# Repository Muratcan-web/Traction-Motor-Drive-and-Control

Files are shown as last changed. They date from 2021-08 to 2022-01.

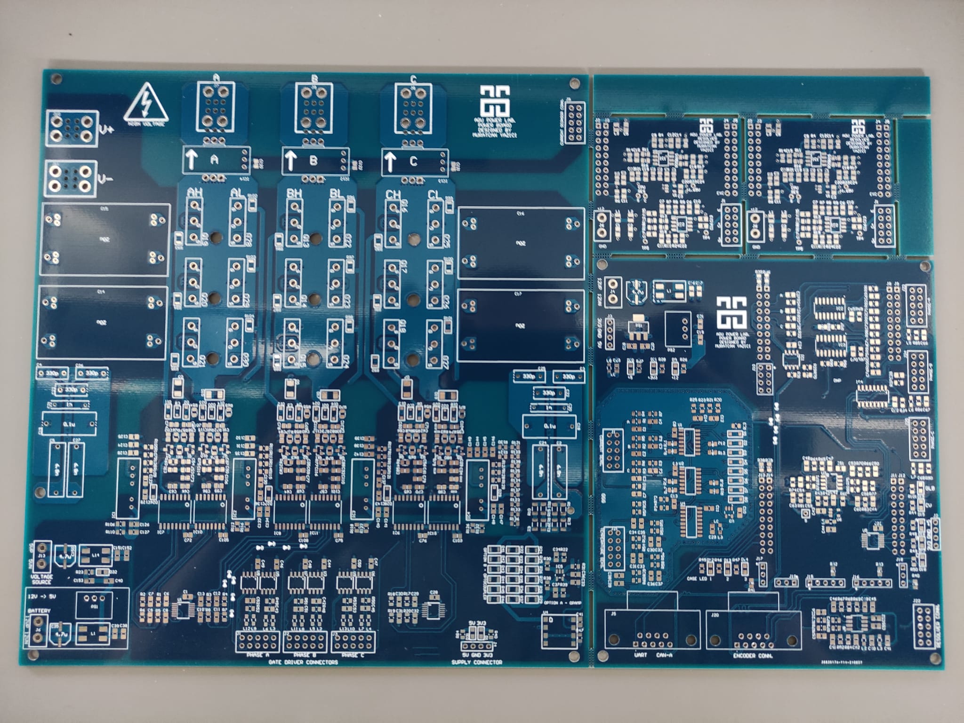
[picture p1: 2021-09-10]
pcb.jpeg

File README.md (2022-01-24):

# Traction-Motor-Drive-and-Control
In this project, I worked on the Control and Power Boards of a Traction Motor Drive system. The drive system is capable of controlling upto 36kW AC Induction Motors. 

You can find the required circuits and layout of the system in this repository. The detailed explanations of the firmware can be found in "TMD Final Report.pdf" document. 

If you have any questions and suggestions, please do no hesitate asking: muratcann.yazici@gmail.com

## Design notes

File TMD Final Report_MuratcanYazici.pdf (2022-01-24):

# Traction Motor Drive Design and Control

Muratcan Yazici
Electrical Electronics Engineering Abdullah Gul University
muratcan.yazici@agu.edu.tr

Dr. Burak Tekgün
Electrical Electronics Engineering Department Abdullah Gul University
burak.tekgun@agu.edu.tr

Abstract— This paper reports a detailed description of a Drive and Control system for Traction Motors. The hardware and software configurations, details and the working principles of each stage are explained in detail.

Keywords— AC Motors, Drive and Control Systems, PI Control, F28379D, PCB Design.

1. INTRODUCTION
Motor drivers act as an interface between the power source and the motor and mainly adjust the speed of the employed motor. These devices provide the users with process control and energy conservation. The aim of an AC Motor Drive is to drive a 3-Phase AC motor. To drive 3-phase motors, “Variable Frequency Drives (VFD)” are employed. VFDs convert an incoming 3 Phase voltage into a variable frequency 3 Phase output and drive AC Motors. The block diagram of a VFD is shown in Figure 1.1.

Figure 1. 1: VFD Block Diagram

In such systems, the first step is to make the AC/DC conversion. The rectifier fulfills this duty. Then, the DC link further filters the rectified voltage and delivers a pure DC voltage to the inverter stage. The inverter converts the DC voltage in to a controlled AC voltage to provide the user with the control of the AC motor torque, speed and position.

In this particular project, the input power is directly a DC voltage. It can be thought of an electric vehicle battery pack. Thus, the rectifier stage in Figure 1.1 is not populated. The particular block diagram of the “Traction Motor Drive Design and Control” project is shown in Figure 1.2.

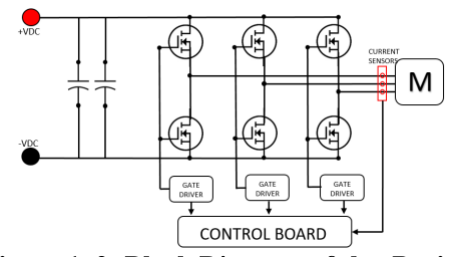
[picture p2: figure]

Figure 1. 2: Block Diagram of the Project

As can be seen from the block diagram, the incoming DC voltage is filtered, and then converted into variable frequency AC voltage at the inverter stage. The inverter is designed using IXFH42N60P3 N-Channel high power MOSFETs. Each phase is controlled by two MOSFETs, and AC output is produced based on the switching of these devices. The switching application of the MOSFETs is controlled by Gate Driver circuits. These circuits take PWM signals from the Control Board and provide the MOSFETs with required switching signals. Thus, the control of the motor is completed with the control signals coming from the control board.

There are Current Sensors (LEM-25) at the input of the motor to check the amount of current that motor uses. The current values for phase A and C are fed back to the control circuit, and the required precautions are calculated and carried out.

The aforementioned process is divided into two PCB boards: Power Board and Control Board. These boards consists of the circuits in Table 1.1. Each of these circuits is explained thoroughly in the following sections.

Control Board | Drive Board
1) Fault Circuit | 1) Bus Voltage Filter
2) Power Supply Interface | 2) Bus Voltage Sense Circuit
3) Current Sensor Interface | 3) Gate Driver Fault Circuit
4) Voltage Sensor Interface | 4) Isolated DCDC Converter Stage for Gate Drivers
5) Temperature Interface | 5) Gate Driver Circuit
6) CAN Interface | 6) Mosfet Connections
7) F28379D Launchpad
8) Gate Driver Interface
9) Resolver Interface
Table 1.1: The contents of each PCB

2. CONTROL BOARD CIRCUIT EXPLANATIONS
2.1. Fault Circuit

This circuit is implemented to shut the operation of the Motor Driver in case of a Over Current or Over Voltage failure. This circuit is used as an external fault detection application in which the current measurements from the current sensors and the DC Bus voltage are checked. This operation is carried out using quadrature comparators, particularly LM339.

The current sensor (LEM LES25-NP) will output a voltage between 0.25V and 4.75V, which represent -85A and +85A respectively. For instance, if the amplitude of the current output is desired to be between -20A and +20A, the output voltages should be in the range of 2V and 3V. The Voltage/Current output graph of the current sensor (LES 25 NP) is depicted in Figure 2.1.1.

Figure 2.1. 1: Voltage/Current relationship of LES 25NP

: Primary Nominal RMS Current (25A)
: Primary Current Measuring Range (-85A to 85A)

Based on the requirement (the currents should not exceed -20A to 20A range) that the output of LES25 should be between ~2V and ~3V, a circuit was built that produces a FAULT signal if the voltage is not in the aforementioned range. To build this circuit, LM339, a low-power comparator is selected. With this device, four different conditions can be analyzed simultaneously. The pin diagram of LM339 is shown in Figure 2.1.2.

Figure 2.1. 2: Pin Diagram of LM339

Comparator circuits simply compare two voltages. The output of such a device is digital (either HIGH or LOW) depending on the voltage values of the inverting and non-inverting inputs. The principle of the operation is that if the voltage value at the inverting input (-) is greater than the non-inverting(+) input, the output is LOW, and vice versa.
The output of the comparator circuit results in a signal, meaning that FAULT = LOW, NO-FAULT = HIGH. The cases are as follows: (Refer to Figure 1.1.5 for the schematic)
- If the output voltage of a Current Sensor (IX_Filtered) is less than LowLimit (2V), which is a faulty case, the output of that condition will be LOW. If IX_Filtered is higher than the LowLimit, which is a non-faulty case, the output will be HIGH.
- If the output voltage of a Current Sensor (IX_Filtered) is less than HighLimit (3V), which is a non-faulty case, the output of that condition will be HIGH. If IX_Filtered is higher than the HighLimit, which is a faulty case, the output will be LOW.

The desired input/output table is shown in Table 2.1. To simulate this operation, the circuit shown in Figure 2.1.3 was set on Proteus, and simulated. The simulation result is shown in Figure 2.1.4.

IX_Filtered (V) | Fault
2< V < 3 | No
3 < V | Yes
V < 2 | Yes
Table 2.1: Desired Current Fault Cases

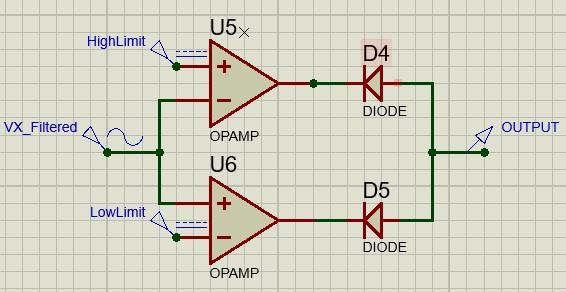
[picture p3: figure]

Figure 2.1. 3: The simulated circuit

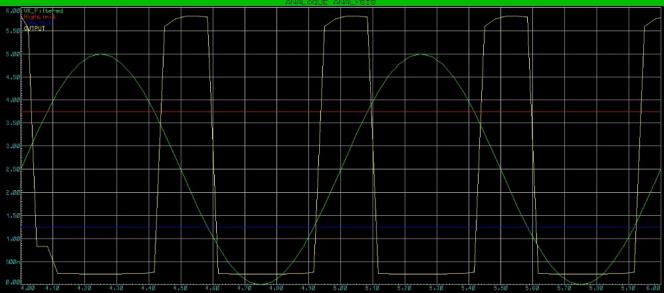
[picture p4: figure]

Figure 2.1. 4: Simulation Results

When IX_Filtered (Green) is in the range of non-faulty voltages, the output (Yellow) is HIGH, else it is LOW. Following this logic, the circuit shown in Figure 2.1.5 and Figure 2.1.6 are designed. In case either one of the fault checks is not needed, the DNP resistors will be populated to create automatically non-fault (HIGH) output.

Figure 2.1. 5: A and B phase Fault Circuit

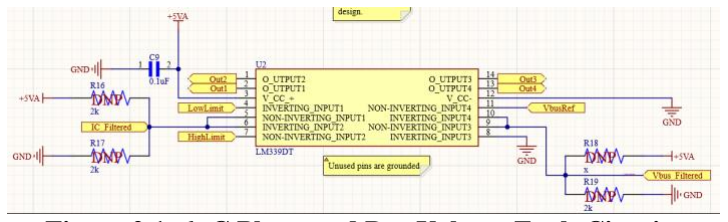
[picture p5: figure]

Figure 2.1. 6: C Phase and Bus Voltage Fault Circuit

In case the control is not required, the resistors must be populated to generate a DC voltage (Voltage divider) in high and low limits so that a non-faulty case will be automatically obtained.

If a VBUS fault check is not required, populating R19 will be enough to disable this function. On the design, the VBUS error limit is 280V. This limit can be arranged.

The reference voltages for the comparator circuit are obtained using the following voltage divider circuitry shown in Figure
2.1.7. The values are only for example, not for the current design. The voltage level must be adjusted to satisfy the need.

Figure 2.1. 7: Reference Voltage Divider Stage

The outputs of the comparator circuits must be connected to Diodes. The reason for that is, when there is a FAULT case, the main fault signal will be tied to the ground. If there is a no-fault case, there will not be a voltage drop on the pull-up resistor shown in Figure 2.1.8 and the input to the inverter will be high. Moreover, since the output of the comparator circuit
is | , an inverter is required for the SR-Latch input. SR-
Latch is required for shutting down the PWM signals, and keeping them shut down until the reset signal (SR-Reset) is sent.

Figure 2.1. 8: Comparator Outputs and Inverter Circuit

At the output of the inverter is a FAULT signal, which is connected to the SR Latch (HEF4043BT). The SR Latch output is connected to Differential Line Driver Enable input for the PWM signals to shut down the operation in case of a failure. The SR Latch Connections are shown in Figure 2.1.9.

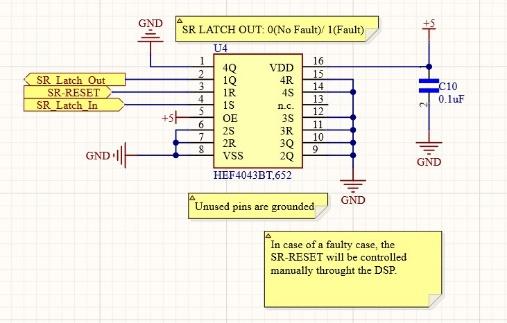
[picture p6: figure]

Figure 2.1. 9: SR Latch Connections

The reset signal is controlled through DSP, and the system is restarted after the fault is eliminated.

To sum up, Fault Circuit is used to control the operation conditions based on the current sensor outputs and VBUS voltage. In case of an overvoltage or undervoltage, the operation will be shut down for protecting rest of the circuits.

2.1.1. Functionality Tests of the Fault Circuit

To test this circuit, the Current Sensor control for phase C is eliminated, meaning that the voltage divider resistors are populated and a 2.5V regulated voltage, which is a non-faulty case, is sent to comparators. The functionality test is run for phase A and B current sensor outputs. As mentioned above, the circuit should yield a faulty output if the current sensor outputs a voltage outside the range of 2V-3V. A sinusoidal wave that has the below features is applied to the circuit, and output is examined. The input is Channel 1 (yellow), and the fault circuit output is Channel 2 (blue). The result is depicted in Figure 2.1.10.

Figure 2.1. 10: Oscilloscope View of the Test Setup

As can be seen, when the input voltage is greater than 3V and less than 2V, the output is low. Otherwise, the output is high. The output is connected to an inverter, and connected to the SR-Latch input. Whenever the fault is generated, SR-Latch remains HIGH untill reset.

2.2. Power Supply Interface

This circuit aims to provide the rest of the circuitry with clean and sufficient power. The input to the supply circuit is 12V battery connections. This voltage should be filtered and converted into 3.3V and 5V to provide the ICs with sufficient power.

Firstly, a common mode choke (CMC) is applied to the battery voltage. Common Mode Noise is present on the circuits mainly due to high-frequency switching applications. High-frequency results in a high di/dt ratio which results in higher Electromagnetic Noise. This noise is present on the signal traces and common ground planes, which affects the signals. The contribution of a CMC to the circuit is that it attenuates the common-mode noise. It adds inductance to the power traces to minimize the current ripples. It is used to reduce the EMI components on the power supply. In addition, to reduce the common-mode noise, power traces are kept as close as possible on the layout. The common-mode choke (ACM7060-701-2PL-TL01) connection is shown in Figure 2.2.1.

Figure 2.2. 1: Common Mode Choke Connections

After filtering the battery power, the 12V should be converted into 3.3V and 5V. First, 12V is converted to 5V with a buck converter (R-78E5.0-1.0), then the 3.3V is obtained by an LDO that has the input from the 5V. Here, a great care is paid for the noise on analog and digital circuits on the Control Board. Analog circuits are more susceptible to noise. Thus, an LC filter is applied and the power lines of analog and digital circuits are separated. Voltage conversion and filter circuits are shown in Figure 2.2.2 and Figure 2.2.3.

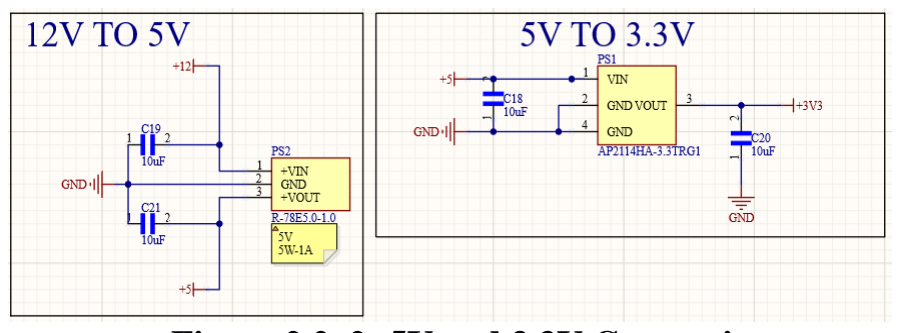
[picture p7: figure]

Figure 2.2. 2: 5V and 3.3V Conversion

Figure 2.2. 3: LC Filter for the Analog Circuits

2.3. Current Sensor Interface

This circuit processes the Current Sensor outputs and sends them to the Fault circuit and DSP. IX_CSensor refers to the output of the current sensor for the associated phase. IX_Filtered is connected to the Fault Circuit for external fault control, and Current-X is connected to DSP. Notice the voltage divider before the Current-X for the protection of the DSP. The current sensor interface circuit is shown in Figure 2.3.1.

Figure 2.3. 1: Current Sensor Interface Circuit

In this part, taking the measurements of two currents will be enough because of Kirchoff’s law. The law ponits out that the sum of the currents entering a node should be zero. Thus:

If the current value for phase A and C is measured, phase B can be reconstructed. Therefore, two current sensors will be enough.

2.4. Voltage Sensor Interface

Voltage values will be found using estimation method from the PWM signals. The XHS_PWM is a modulated signal, and it is demodulated for DSP to read it using the low-pass filter. This circuit is shown in Figure 2.4.1.

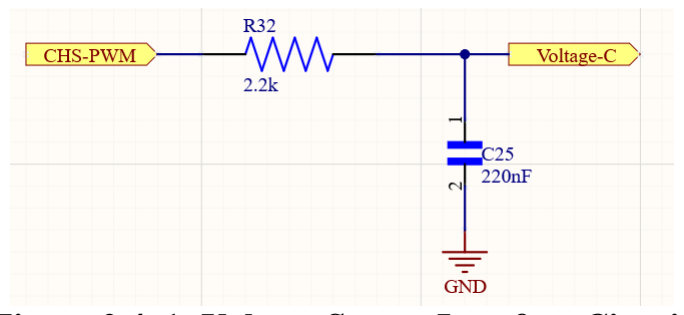
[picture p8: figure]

Figure 2.4. 1: Voltage Sensor Interface Circuit

2.5. Temperature Sensor Interface

This circuit is used to obtain the temperature of Bus capacitors, Bus Bar, and three IGBTs. The output of the thermistor is filtered in the interface circuit and sent to DSP for control. The connector connections of the temperature sensor interface are shown in Figure 2.5.1, and the circuit is shown in Figure 2.5.2.

Figure 2.5. 1: The External Connectors

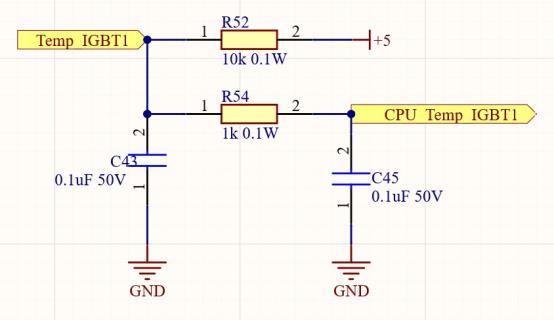
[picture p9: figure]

Figure 2.5. 2: Temperature Sensor Interface Circuit

2.6. CAN Bus Interface

This circuit is used for CAN Bus lines (CANH and CANL) to be converted to TX and RX signals via a CAN Transceiver. The CAN Transceiver connections are shown in Figure 2.6.1.

Figure 2.6. 1: CAN Bus Interface Circuit

CAN Transceivers convert the differential CAN pair (CANH and CANL) into TX (transmit) and RX (receive) signals. CANH and CANL signals are separated from each other by a terminating resistor, 120-ohms. There can not be a direct connection between CANH-L pair and an MCU. Transceivers converts them into TX and RX. TX and RX signals are connected to MCUs (TX to RX/ RX to TX).

2.7. F28379D Connections

The main controller board that sends the control signals to the controller is F28379D Launchpad. The software provides the system with the required signals. It has several connectors on the Launchpad, and requires a couple of hardware configurations.

2.7.1. Global Fault Signal

There are two FAULT circuits in this controller board. The first one is the fault circuit for the current sensor and bus voltage (refer to section 2). The output of this circuit is
CVSense_Fault ( | ).

The second one is the Gate Driver fault outputs (X-FAULT).
These signals are also | In case of faulty case, the
corresponding LEDs will turn ON.

In order to manage all the FAULT signals as one output, a quadrature AND Gate is employed. If any of CVSense_Fault or X-FAULT are faulty (LOW), the AND gate will have LOW signal at the output. This brings us to the conclusion that the
AND Gate output is also | A HIGH signal is generated
only if all the Fault signals are HIGH. The Global Fault circuit is shown in Figure 2.7.1.1.

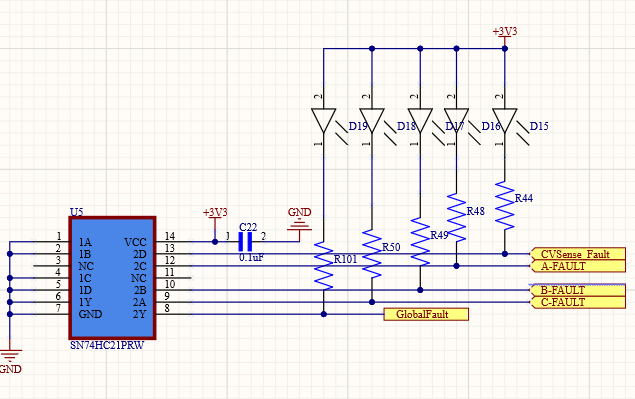
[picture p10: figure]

Figure 2.7.1. 1: Global Fault AND Gate Circuit

2.7.2. DSP Connectors

The Connector designators on Altium Schematics and the actual designators on Launchpad do not match. See the notes next to the connectors to locate the actual connectors on the DSP. In Figure 2.7.2.1, the connectors for Quadrature encoders, ground, and CAN-B Bus connections are presented. For all the power connections (3.3V, 5V), 0-ohm DNP resistors are placed. The reason for these DNP resistors is that the DSP will be either powered by the USB cable provided in the package or the power line from the power circuit. When the DSP is powered by the USB cable, the power from an external circuit is not necessary, thus the DNP resistors shall not be populated. In case it is desired to power the DSP by the power supply existing on the board, the 0-ohm resistors must be populated.

Figure 2.7.2. 1: QEX and Power Connections

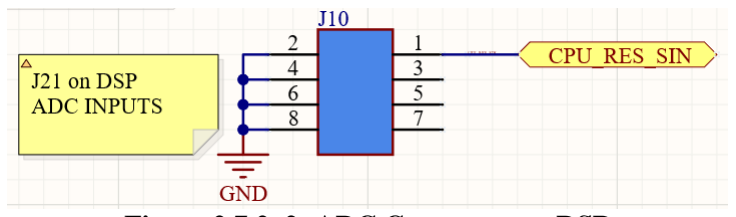
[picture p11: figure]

Figure 2.7.2. 2: ADC Connector on DSP

Figure 2.7.2. 3: AUX Connector

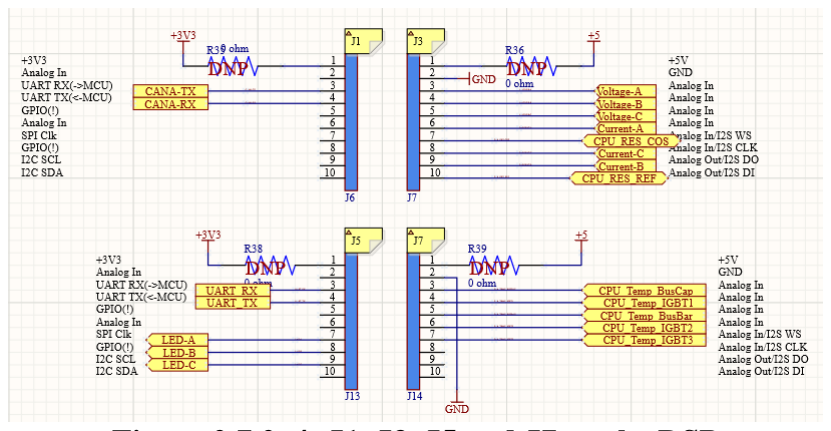
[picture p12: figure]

Figure 2.7.2. 4: J1, J3, J5 and J7 on the DSP

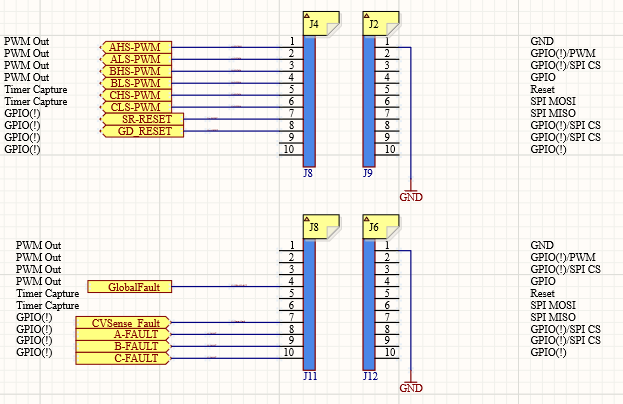
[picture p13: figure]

Figure 2.7.2. 5: J4, J2, J8 and J6 on the DSP

2.8. Gate Driver Interface Circuit

Signal integrity has the utmost importance when controlling power devices with a gate driver. Gate drivers are susceptible to EMI or any noise generated by power devices. Power devices have extremely high switching frequencies and create dense EMI which can easily couple on gate control signals. To prevent any interference, differential signals are used for this gate driver design.

Differential signals reduce the effect of the noise that is created during the switching events. A single-ended signal can be converted into a differential pair by transmitting both the original signal and its complement in two closely coupled wires. Thereafter, these two signals are compared to reconstruct the original signal. In Figure 2.8.1, the noise immunity of differential signals and reconstruction of the original signal from the differential pair is depicted.

Figure 2.8. 1: Noise Cancellation of Differential Signals

In the circuit, the differential pairs for XHS-PWM, XLS-PWM are constructed using AM26LV31EIPWR quadruple differential line drivers. The associated circuit is shown in Figure 2.8.2 and Figure 2.8.3.

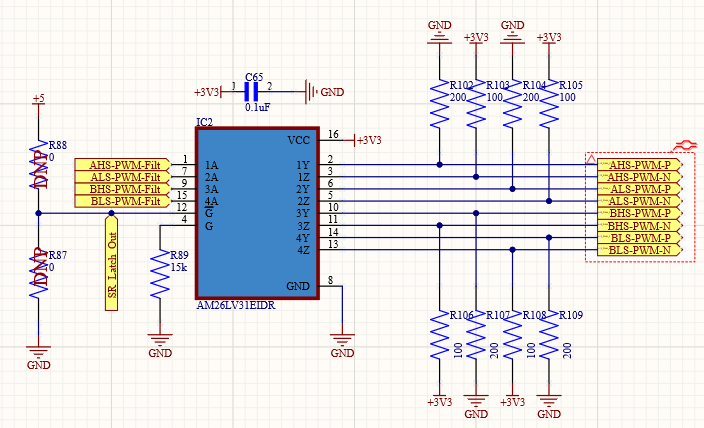
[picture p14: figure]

Figure 2.8. 2: Differential Signal Construction (Phase A and B)

Figure 2.8. 3: Differential Signal Construction (Phase C)

SR Latch Output is connected to these differential line driver ICs. In a faulty situation, SR Latch Out will be HIGH. G' will be controlled by SR Signal. If Faulty Signal comes (SR HIGH), G' will go High and the IC will be disabled.

Also, differential FAULT signals are coming from the Gate Drivers via the connectors. These X-FAULT-P and X-FAULT-N signals are connected from the gate driver circuit (Power Board) to the gate driver interface circuit (Control Board). Connector diagrams are shown in Figure 2.8.4.

Figure 2.8. 4: Gate Driver Interface Connector

As such, the differential fault signals are reconstructed using a differential line receiver. The operation is shown in Figure 2.8.5.

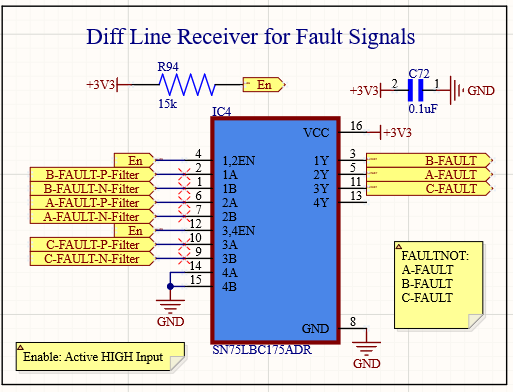
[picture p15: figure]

Figure 2.8. 5: Differential Line Receiver Circuit

2.8. Resolver Interface

Resolvers and encoders are devices that measure the rotary position of a shaft by converting the mechanical motion into an electrical signal.
Resolvers have a primary winding on the rotor, and two secondary windings on the stator. Simple structure of a resolver is shown in Figure 2.9.1.

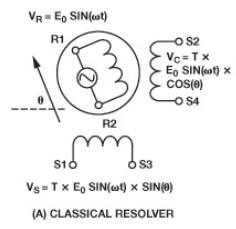
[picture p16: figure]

Figure 2.9. 1: Resolver Structure

When the primary winding is excited (RES_REF_OUT on control board), a signal is induced to the secondary windings. The amount of coupling is a function of the rotor position and the resolver attenuation factor. The secondary windings are mechanically 90 degree apart from each other. This yields a 90 degree phase shift between the secondary windings. To have a better understanding, the mathematical formulas below shall be analysed:

As mentioned above, a sine wave excites the primary winding and two output signals are induced on the secondary windings. To read these output signals, a Resolver to Digital Converter (RDC) is needed. RDC uses the modulated sine and cosine signals to decode the rotor position.
However, the resolver attenuates the output voltage and it is hard to perform the conversion on such a signal. The signal should be amplified first. Also, resolvers are used in noisy environments, and the environment may induce high-frequency noise to the output signal. Thus, the signal should be filtered as well. The circuitry used to amplify cosine and sine feedbacks are shown in Figure 2.9.2. The same circuit is also populated for Sin output.

Figure 2.9. 2: Resolver Cosine Feedback Interface Circuit

A similar procedure is also applied for the excitation signal. This signal is generated by F28379D, and needs to be amplified. The circuit that fulfills this duty is shown in Figure
2.9.3. Also, the DC offset is eliminated at the output.

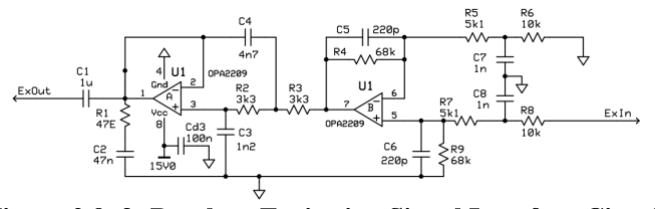
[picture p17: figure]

Figure 2.9. 3: Resolver Excitation Signal Interface Circuit

As mentioned above, the Resolver returns two outputs back. One is sine and other is cosine signal outputs. These two outputs are modulated by the excitation signal. The excitation signal and the modulated signal are shown in Figure 2.9.4.

Figure 2.9. 4: Excitation and Feedback Signals

The experiment result of the working principle above is shown in Figure 2.9.5.

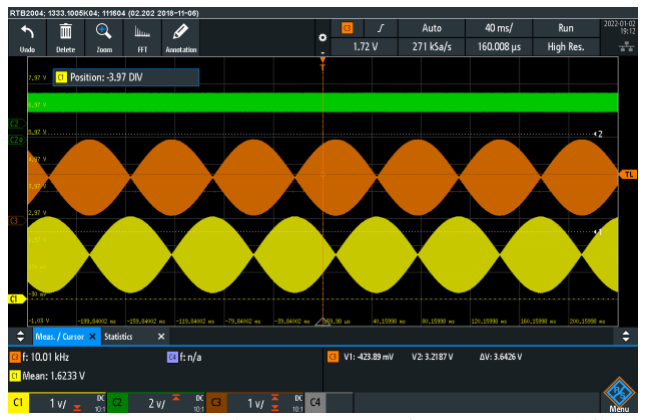
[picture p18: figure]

Figure 2.9. 5: Experiment Result of the Resolver (CH1: Sine Feedback, CH2: Excitation Signal, CH3: Cosine Feedback)

The position of the motor can be extracted by finding the amplitude of the sine and cosine envelops. The amplitude changes as the motor turns, and there is a 90 degree shift between sine and cosine feedbacks.
Also, the reference speed and the measured speed is verified using Figure 2.9.6.

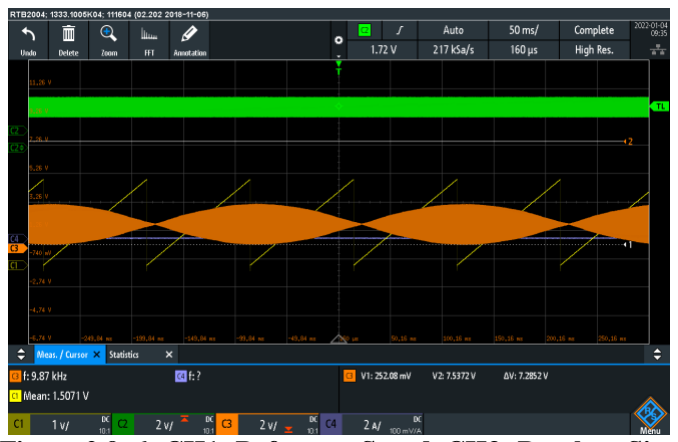
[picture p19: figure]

Figure 2.9. 6: CH1: Reference Speed, CH3: Resolver Sine Feedback

When the motor turns a full turn (2π radian or 360 degrees), sine feedback completes a period. And each triangular shape in CH1 (reference speed) represents 90 degrees of rotation, meaning that four repetitions respresent a complete turn of the rotor. There is a small phase shift between them, yet it still verifies that the resolver feeds back the rotor position correctly.

One of the benefits of a resolver is their lack of sensitive optics, which allows them to withstand higher vibrations and shock loads than encoders. They are also resistant to the electrical disturbances, can withstand higher temperatures.

3. POWER BOARD CIRCUIT EXPLANATIONS
3.1. DC Bus Filter

EMI filters are placed after the DC Power supply (B+, B-)in order the filter out the EMI and other interferences that are present on the power. This stage is crucial for the accuracy and precision of all the circuitry on the board. The filtering stage is shown in Figure 3.1.1.

Figure 3.1. 1: Bus Voltage Filter

At the start and the end of the Filtering are Y Caps. Y Caps are designed to filter out the common-mode noise and are connected between the line and chassis. These caps filter the coupling between the ground and the power line. It is extremely critical for these caps not to be short-circuited since it will create a shock risk for the users.
It is important to note that the voltage limits for these CAPS should be high enough to withstand the amount of power (+400DC). All the capacitors in the EMI circuit are film caps, which often have higher voltage limits.
The resistors after the first Y-Caps stage are placed there to absorb the high energy. When the high voltage is charged to the film caps, it does not discharge immediately and keeps the voltage there. The populated resistors help the discharge application.

The 20uF caps are employed to filter out the lower frequency ripples. After that, there are pairs of 0.1uF, 1nF, and 330pF capacitors for precise high-frequency filtering. Three different capacitance values are used for filtering the higher frequencies better. Capacitors have different impedances depending on the frequency, and their filtering capacity varies. The Impedance-Frequency graph of capacitors based on different capacitance values is shown in Figure 2.1.2. The impedance of a capacitor is calculated as follows:

Thus, placing different capacitors provides the system with enhanced filtering capacity. There are two caps in the system. These caps will be put at the sides of the board symmetrically. The capacitors actually include a series LCR branch in them. At certain frequencies, the impedance of the inductor and the capacitor is equal and the total impedance of the capacitor is minimum. This point is called the resonance point, where the capacitor has the highest filtering capability. By applying different capacitors, the filtering capacity of the system is enhanced.

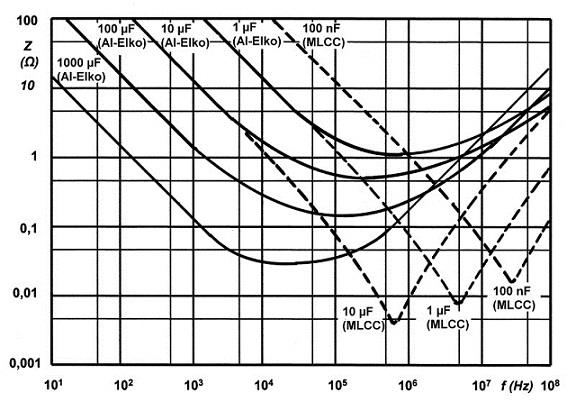
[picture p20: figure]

Figure 3.1. 2: Impedance vs Frequency of Different Capacitor Values

3.2. DC Bus Voltage Sense Circuit

V Bus voltage measurement is important to track the operation conditions of the system. A high voltage is first scaled down to a 0-3V band and then sent to the DSP. For this operation, there are two options in the design. These options are shown in Figure 3.3.1 and Figure 3.3.2.

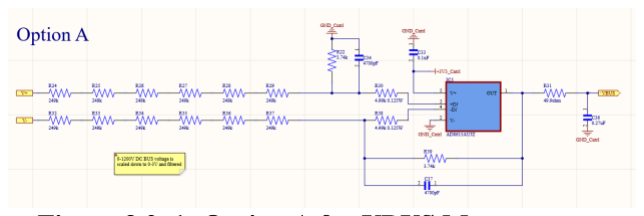
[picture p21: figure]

Figure 3.2. 1: Option A for VBUS Measurement

In this option, the high voltage is scaled down to a low voltage using the resistors and then the filtering is applied. VBUS port is connected to the fault circuit interface. If the VBUS is greater than the VBUS reference, a fault is indicated.

Figure 3.2. 2: Option B for VBUS Measurement

In this option, the same voltage scaling method was applied, yet this time the voltage measurement is isolated from the incoming voltage side.

Currently, option A is populated on the PCBs. In this option, the voltage is scaled using the following voltage division formula:

This formula is verified on the system by taking measurements at different VBUS levels up to 60V. The scaled VBUS versus the actual VBUS voltage plot is shown in Figure 3.3.3.

Figure 3.2. 3: Scaled and Actual VBUS Voltages

In this design, the maximum allowed VBUS is, say, 280V. It is equivalent to 716mV in the scaled basis. Thus, the VBUS REF voltage in the FAULT circuit must be set to 716mV. If another VBUS limit is desired, the reference voltage must be arranged accordingly. In this design, the VBUS REF is set to 716mV.

3.3. Gate Driver Fault Circuit
The | is generated based on the RDY and /FLT
outputs of the Gate Drivers. Each Gate Driver produces a RDY and a /FLT output.

RDY: Open-drain output to report the correct operation of the device (RDY = high if both chips are above the UVLO level and the internal chip transmission is faultless). Meaning that, 0 is Faulty and 1 is Non-faulty case.
/FLT: Open-drain output to report a desaturation error of the MOSFET (/FLT is low if desaturation occurs). Meaning that, 0 is Faulty and 1 is Non-faulty case.

For each phase, two gate drivers are employed (High Side and Low Side). Thus, there will be four fault signals to generate a main fault signal for each phase. These signals are connected
to a quadrature AND Gate to produce a main | signal.
The AND Gate stage for Phase-C is shown in Figure 3.2.1.

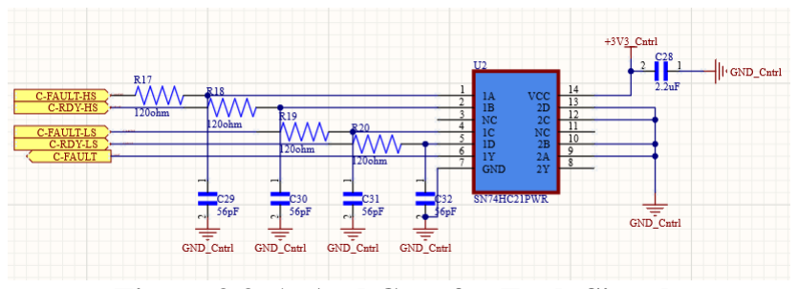
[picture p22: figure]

Figure 3.3. 1: And Gate for Fault Signals

The output signal is X-FAULT, which is then connected to a differential line driver to produce X-FAULT-P and X-FAULT-N differential pair. This differential pair is tied up to the connector to be sent to Controller Board Gate Driver Interface. The differential pair in the control board is then connected to a Differential Line receiver to reconstruct the
original | signals. These | signals are sent to
Global Fault generator circuit. This process is repeated for all three phases (A, B, C). At the end, Fault signals are named as A-FAULT, B-FAULT and C-FAULT. On the Gate driver Circuit, a different type of IC is used for differential line driver and receiver application. SN75179BDR functions as both driver and receiver. Its functional block diagram is shown in Figure 3.2.2.

Figure 3.3. 2: Functional Block Diagram of SN75179DR

Differential HS and LS PWM signal are coming from the controller board via the connector, and differential FAULT signal is sent to controller board via the same connector. To suit this application, SN75179BDR is employed with the following circuit in Figure 3.2.3.

Figure 3.3. 3: Differential Line Driver/ Receiver Circuit

As can be seen, High Side and Low Side PWM differential signals are connected to the receiver inputs after an LCR filter to reconstruct the original PWM signals. These PWM signals are connected to Gate Drivers. Single ended FAULT signal is connected to line driver to produce a differential FAULT signal to be sent to the controller board.

3.4. Gate Driver Fault Circuit

A gate driver is a buffer circuit that amplifies a low voltage low current control signal into a high voltage high current signal. The amplification is necessary since a power transistor would not efficiently work under low voltage. The power transistor requires a certain amount of voltage amplitude at its gate to perform switching. Thus, gate driver circuit is used to amplify a control signal from a microcontroller to make it suitable for efficient and effective operation of semcionductor switchers. Also, gate drivers provide the isolation for switching devices. The operation can be seen in Figure 3.5.1.

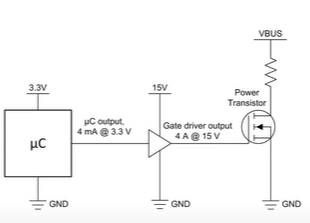
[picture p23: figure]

Figure 3.5. 1: Gate Driver Operation

In this aplication, an isolated gate driver IC (1ED020I12-F2) is empoyed. This IC is a single channel driver for 600/1200V MOSFETs, capable of providing the rail to rail current output with 2A, having Vcesat detection and active miller clamp. Keep in mind that the selected MOSFET for this design is IXFH42N60P3, which can work upto 600V and 42A. 1ED020I12-F2 provides several protection features including MOSFET desaturation protection and active miller clamping. Due to the aforementioned features, 1ED020I12-F2 is suitable for this AC Motor drives. The pin configuration of 1ED020I12-F2 is shown in Figure 3.5.2.

Figure 3.5. 2: Pin Configuration of 1ED020I12-F2

GND1 is the ground of input side.

IN+ is the non-inverting driver input. It controls the driver output if IN- is set LOW. In this design IN- is set LOW to control the output with IN+. An internal pull-down resisor ensures the MOSFET’s Off-State.

IN- is the inverting driver input. It is tied to GND1 to make use of IN+.

/RST is the reset input. It has two functions:
1. Enable/ Shutdown of the input chip. The MOSFET is off if /RST is low.
2. Resets the fault states if /RST is low for a time .

/FLT is the fault output. It reports the MOSFET desaturation error. If an error is present, the /FLT goes LOW (Active Low signal). This pin is connected to Fault circuitry.

RDY is the ready status output to report the correct operation of the 1ED020I12-F2. The RDY goes HIGH if the device operates witout errors (Active high signal).

VCC1 is 5V power supply for the input side.

VCC2 is postivie power supply for output side.

VEE2 is the negative power supply or the output side. In this design, it is connected to -2.7V.

GND2 is the ground for the output side. In this design, it is connected to the negative VBUS voltage.

DESAT is the desaturation detection input. Desaturation is a voltage buildup across the Drain/ Source or Collector/ Emitter while the device is on. It can be caused by power supply short circuits due to faulty wiring, control signal failures, overloads induced by the load and failures in the gate driver circuitry. During desaturation, the current and power dissipation drastically increases. This situation yields a high temperature resulting in the failure of the device. To prevent this, DESAT pin turns off the MOSFETs.
If OUT is high, Vds is above a defined value and the certain blanking time is expired, the desaturation protection is activated and the MOSFET is turned off. When the DESAT voltage reaches 9V, the output is driven low, /FLT is driven low after DEAT to FAULT off delay. This delay can be controlled by an external capacitor.

CLAMP is the miller effect prevention pin. Miller effect is the situation where a parasitic turn-on occurs. During turn-on, the parasitic capacitance between Gate and Drain is charged. When the mosfet is in off state, this capacitor discharges. If the voltage drop across the gate resistor is above a certain value, the parasitic turn-on occurs. This might yield a control error, which can cause short ciruits. During turn-off, the gate voltage is monitored, and the clamp output is activated if the gate voltage drops 2V below the VEE2. If an appropriate negative supply is used, connecting CLAMP to gate it redundant. Therefore, miller clamp feature is disabled in this design. If the unipolar supply is used instead of bipolar supply, the CLAMP should be directly connected to gate of the mosfet.
OUT is the driver output to drive the mosfets. The voltage is switched between VCC2 and VEE2. In normal operation mode, the output is controlled by IN+, and /RST. During error mode (Under voltage lock out (UVLO), internall error or DESAT), output is set to VEE2 independent of IN+.

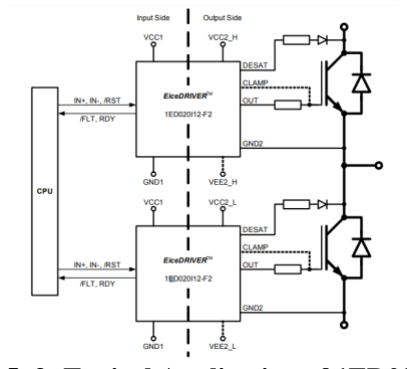
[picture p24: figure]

Figure 3.5. 3: Typical Application of 1ED020I12-F2

Gate driver circuits for High Side and Low side are shown in Figure 3.5.3 and Figure 3.5.4. Refer to the datasheet for the pin functionality. The Gate Driver IC is capable of supplying 2A to the driving MOSFETS. With the built push-pull BJT circuit, this current capacity is increased to 4A. The NPN and PNP BJTs are used for amplifying the MOSFET driving currents in case a higher current is required for the power mosfets.

Figure 3.5. 4: High Side Driver Connections

Figure 3.5. 5: Low Side Gate Driver Connections

3.6. Mosfet and Current Sensor Connections

The driving MOSFET connections for Phase A is shown in Figure 3.6.1. The same process is applied for other Phases as well. There are 3 MOSFETs in parallel to provide higher current if required. However, additional MOSFETs might not be populated if max 42A is enough.

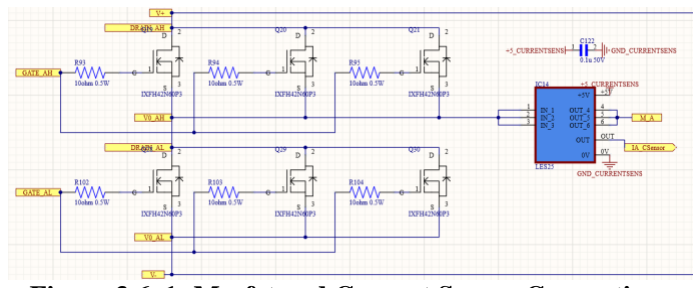
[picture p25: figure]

Figure 3.6. 1: Mosfet and Current Sensor Connections

The selected current sensor for this application is LES 25-NP. This sensor allows user to measure the amount of current that flows into the motor. This component will be populated for two of the phases, allowing two current measurements. The third phase current will be estimated based on the other two measurements.
LES 25-NP is capable of measuring -85A and 85A range. The output voltage is between 0.25V and 4.75V, having 0A at 2.5V. Output voltage of LES 25-NP is shown in Figure 3.6.2. Two current sensors will be populated, and the other phase current will be calculated through Kirchoff’s Law.

Figure 3.6. 2: Input/ Output Relationship of LES 25-P

4. FIELD ORIENTED CONTROL ALGORITHM
The ultimate aim of the vector control is to control the flux producing and torque producing currents separately as in DC motor. These parameters are decoupled so that they can be controlled independently. To fulfill the decoupling, a couple of mathematical transformations are performed by a Digital Signal Processor (DSP). The particular DSP used in this project is TI-LAUNCHXLF28379D which can perform such mathematical conversion fast enough to provide the precise control of a PMSM.

Torque is defined as the cross-product of the stator current and the rotor flux.

As mentioned in the introduction of this section, if these two parameters are kept orthogonal at all times, the produced torque is kept at a maximum. To perform this task, the rotor position is measured by a resolver. The detailed hardware description of the vector control is explained in Control Board Circuit Explanations.

This project takes the “Sensored Field Oriented Control of 3-Phase Permanent Magnet Synchronous Motors using F28379x” as the reference and follows the same control algorithm and descriptions made in their reference manual. The remaining details should be read carefully from this document for a better understanding of the Vector Control. The incremental build in the aforementioned report is followed step by step to realize the closed-loop control.

References:
[1] Akin, B., & Bhardwaj, M. (2013). Sensorless Field Oriented Control of 3-Phase Permanent Magnet Synchronous Motors. Texas Instruments.
[2] Chen, H. L., & Keong, C. (2011, May 1). Keeping Inverters Safe. Electronics Design: https://www.electronicdesign.com/technologies/power-electronics-systems/article/21193243/keepinginverters-safe adresinden alındı
[3] Texas Instruments, (2015). Design Drive Development Kit IDDK v2.2.1 Hardware. Texas Instruments.
[4] Texas Instruments, (2015). Industrial Drives Development Kit Schematics. Texas KInstruments.
[5] Larimore, B. (tarih yok). Sensored Field Oriented Control of 3-Phase Permanen Magnet Synchronous Motors using F28379x. Texas Instruments Inc., C2000 Systems and Applications.
[6] Szymczak, J. (tarih yok). Precision Resolver-to-Digital Converter Measures Angular Position and Velocity. Analog Devices:
https://www.analog.com/en/analogdialogue/articles/precision-rtdc-measures-angularposition-and-velocity.html

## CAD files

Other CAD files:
IDDK_PM_Servo_F2837x/F2837x_RAM/F2837xD_PieCtrl.obj
IDDK_PM_Servo_F2837x/F2837x_RAM/utility Src Files/DLOG_4CH_F.obj
IDDK_PM_Servo_F2837x/F2837x_RAM/F2837xD_SysCtrl.obj
IDDK_PM_Servo_F2837x/F2837x_RAM/IDDK_MuratV3.obj
IDDK_PM_Servo_F2837x/F2837x_RAM/F2837xD_sdfm_drivers.obj
IDDK_PM_Servo_F2837x/F2837x_RAM/F2837xD_Gpio.obj
IDDK_PM_Servo_F2837x/F2837x_RAM/F2837xD_usDelay.obj
IDDK_PM_Servo_F2837x/F2837x_RAM/F2837xD_CodeStartBranch.obj
IDDK_PM_Servo_F2837x/F2837x_RAM/F2837xD_GlobalVariableDefs.obj
IDDK_PM_Servo_F2837x/F2837x_RAM/F2837xD_EPwm.obj
IDDK_PM_Servo_F2837x/F2837x_RAM/F2837xD_PieVect.obj
IDDK_PM_Servo_F2837x/F2837x_RAM/F2837xD_DefaultISR.obj
IDDK_PM_Servo_F2837x/F2837x_RAM/resolver.obj

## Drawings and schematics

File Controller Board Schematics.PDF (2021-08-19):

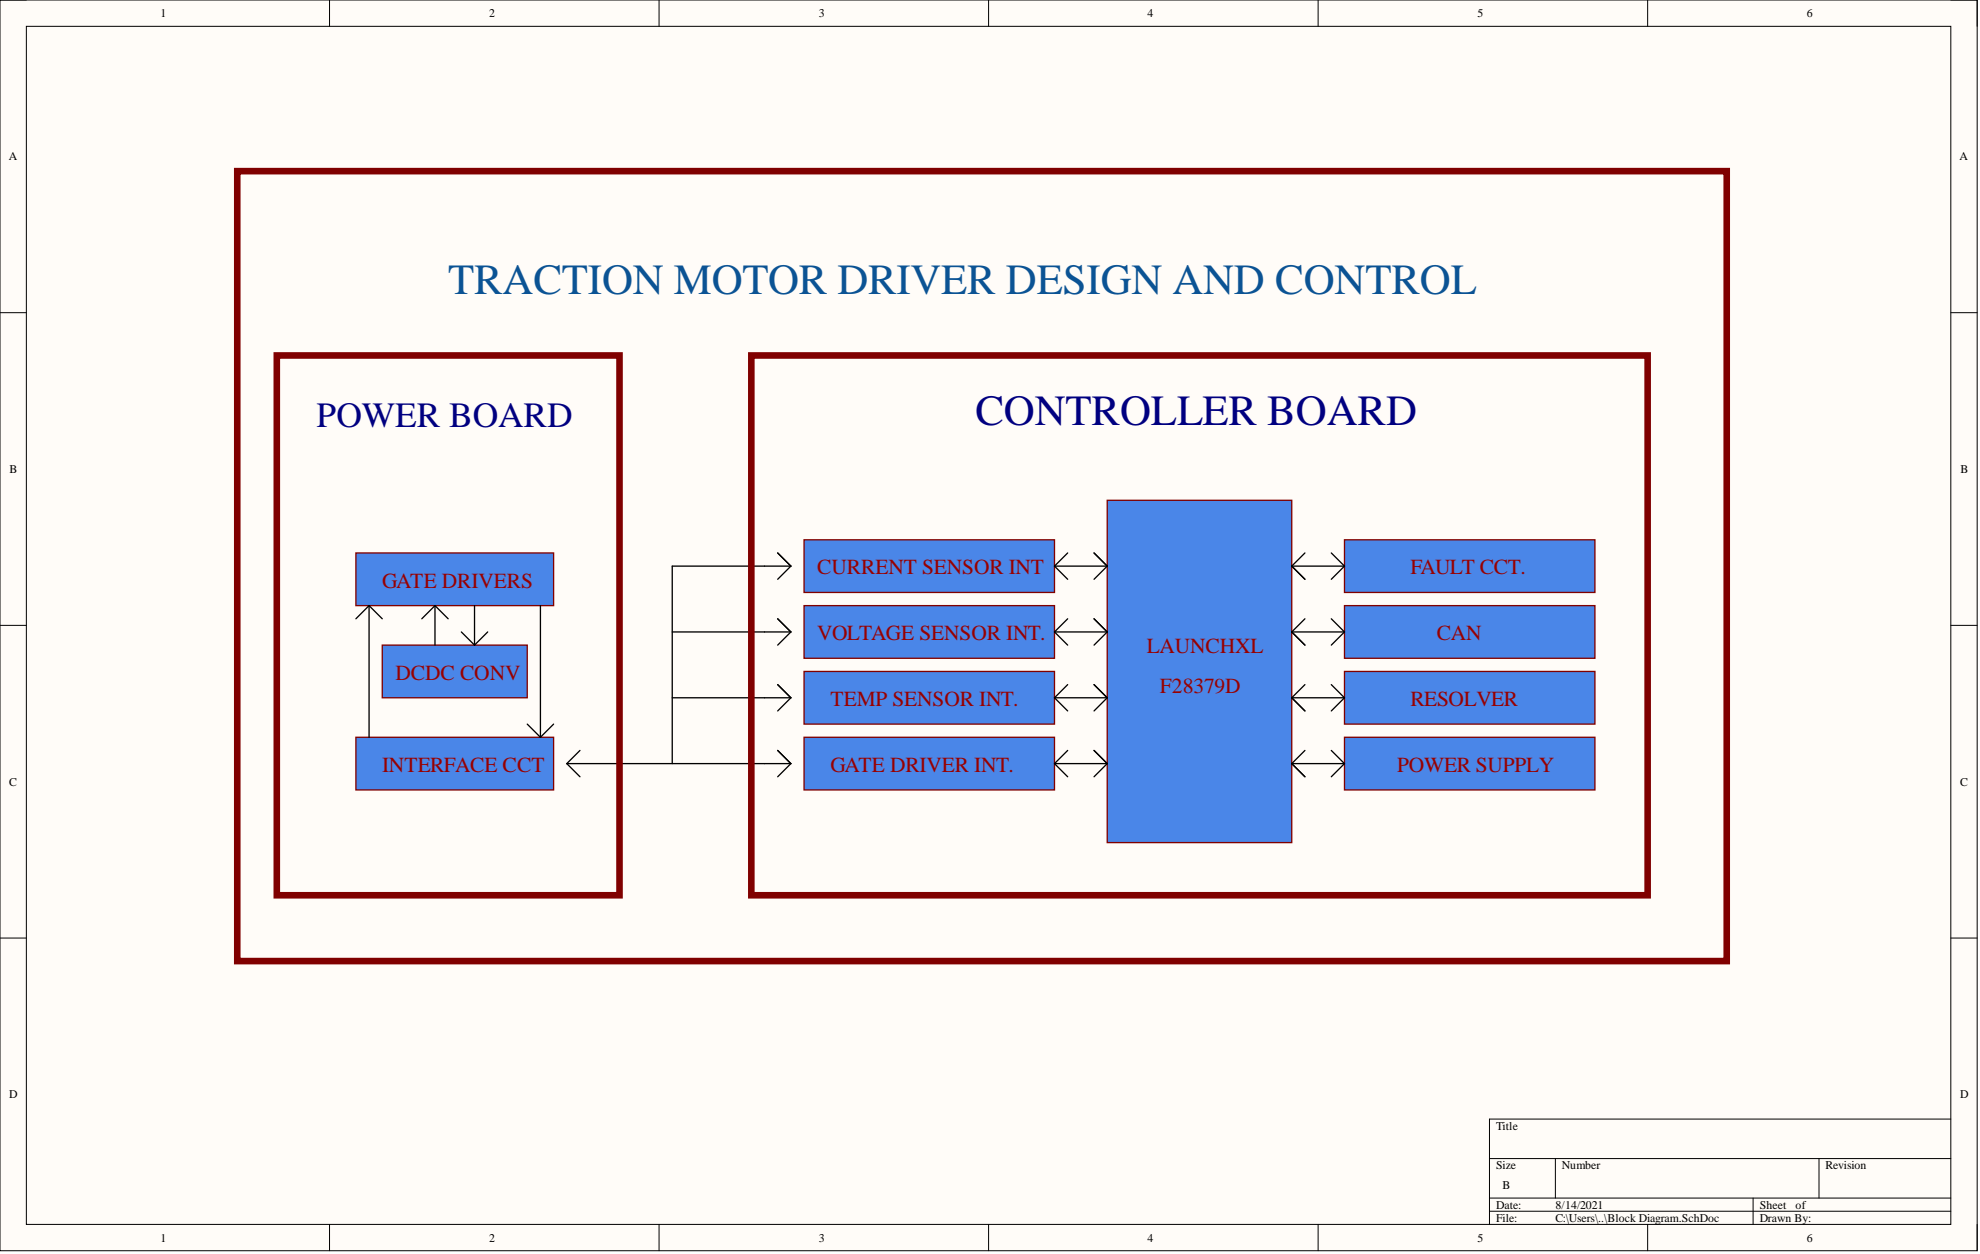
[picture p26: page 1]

TRACTION MOTOR DRIVER DESIGN AND CONTROL

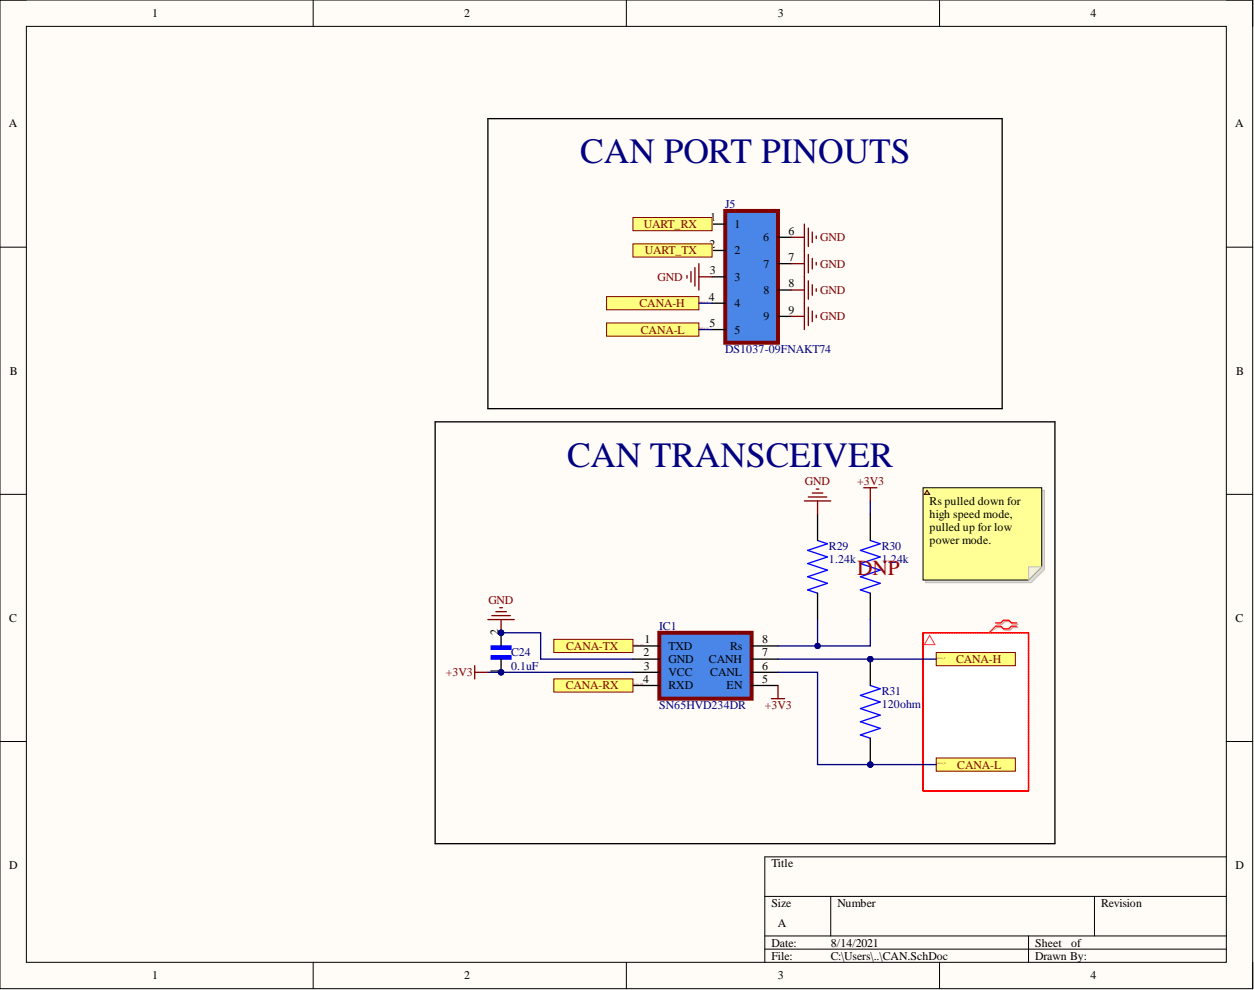
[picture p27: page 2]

Rs pulled down for
high speed mode,
pulled up for low
power mode.

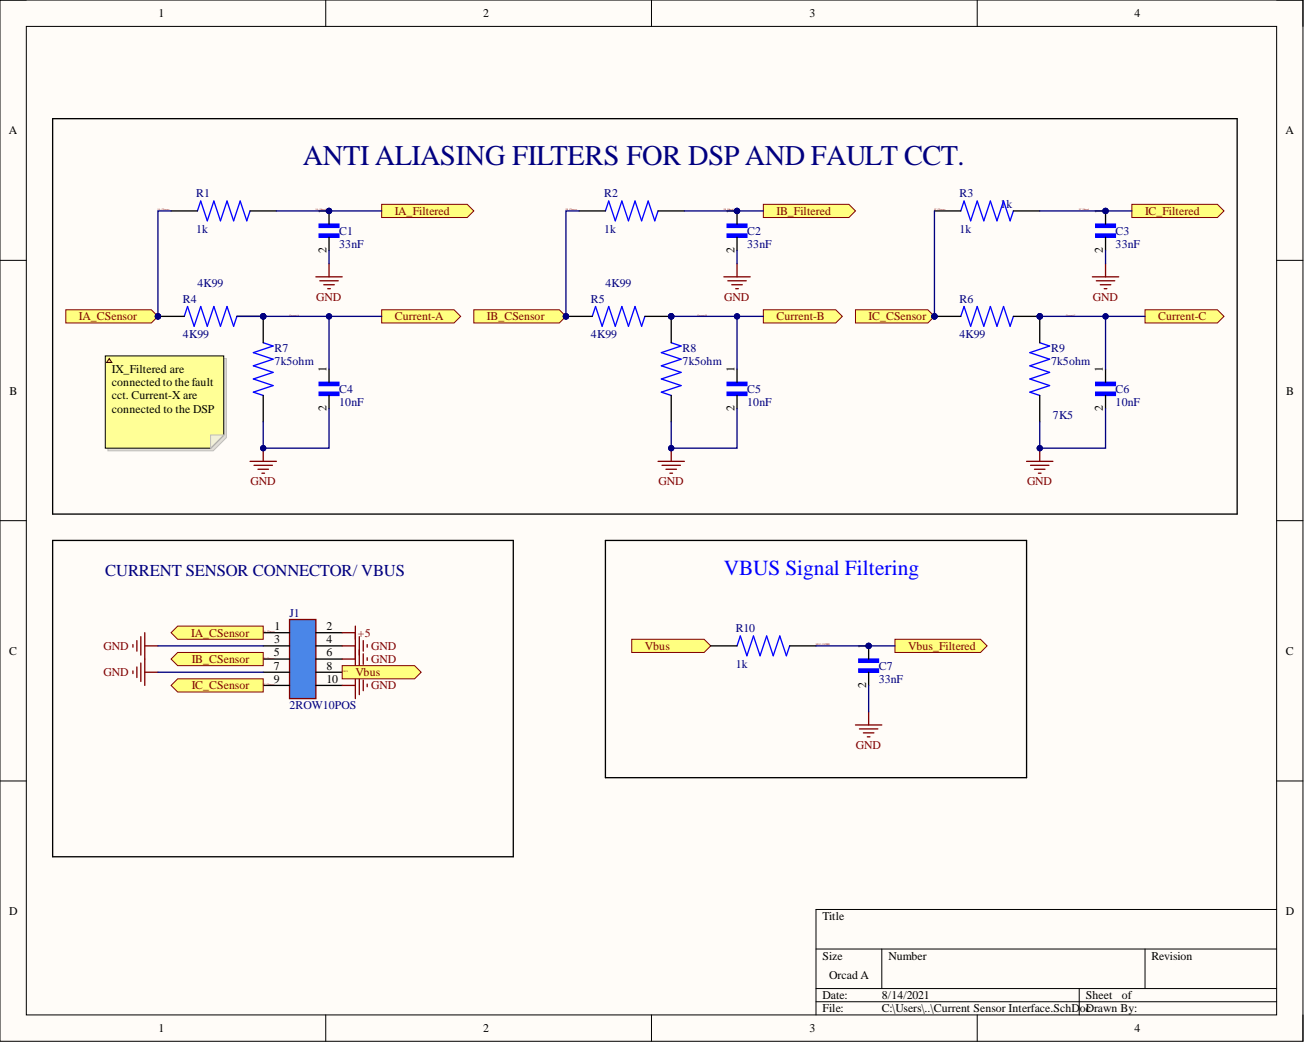
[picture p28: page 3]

ANTI ALIASING FILTERS FOR DSP AND FAULT CCT.

IX_Filtered are
connected to the fault
cct. Current-X are
connected to the DSP

CURRENT SENSOR CONNECTOR/ VBUS

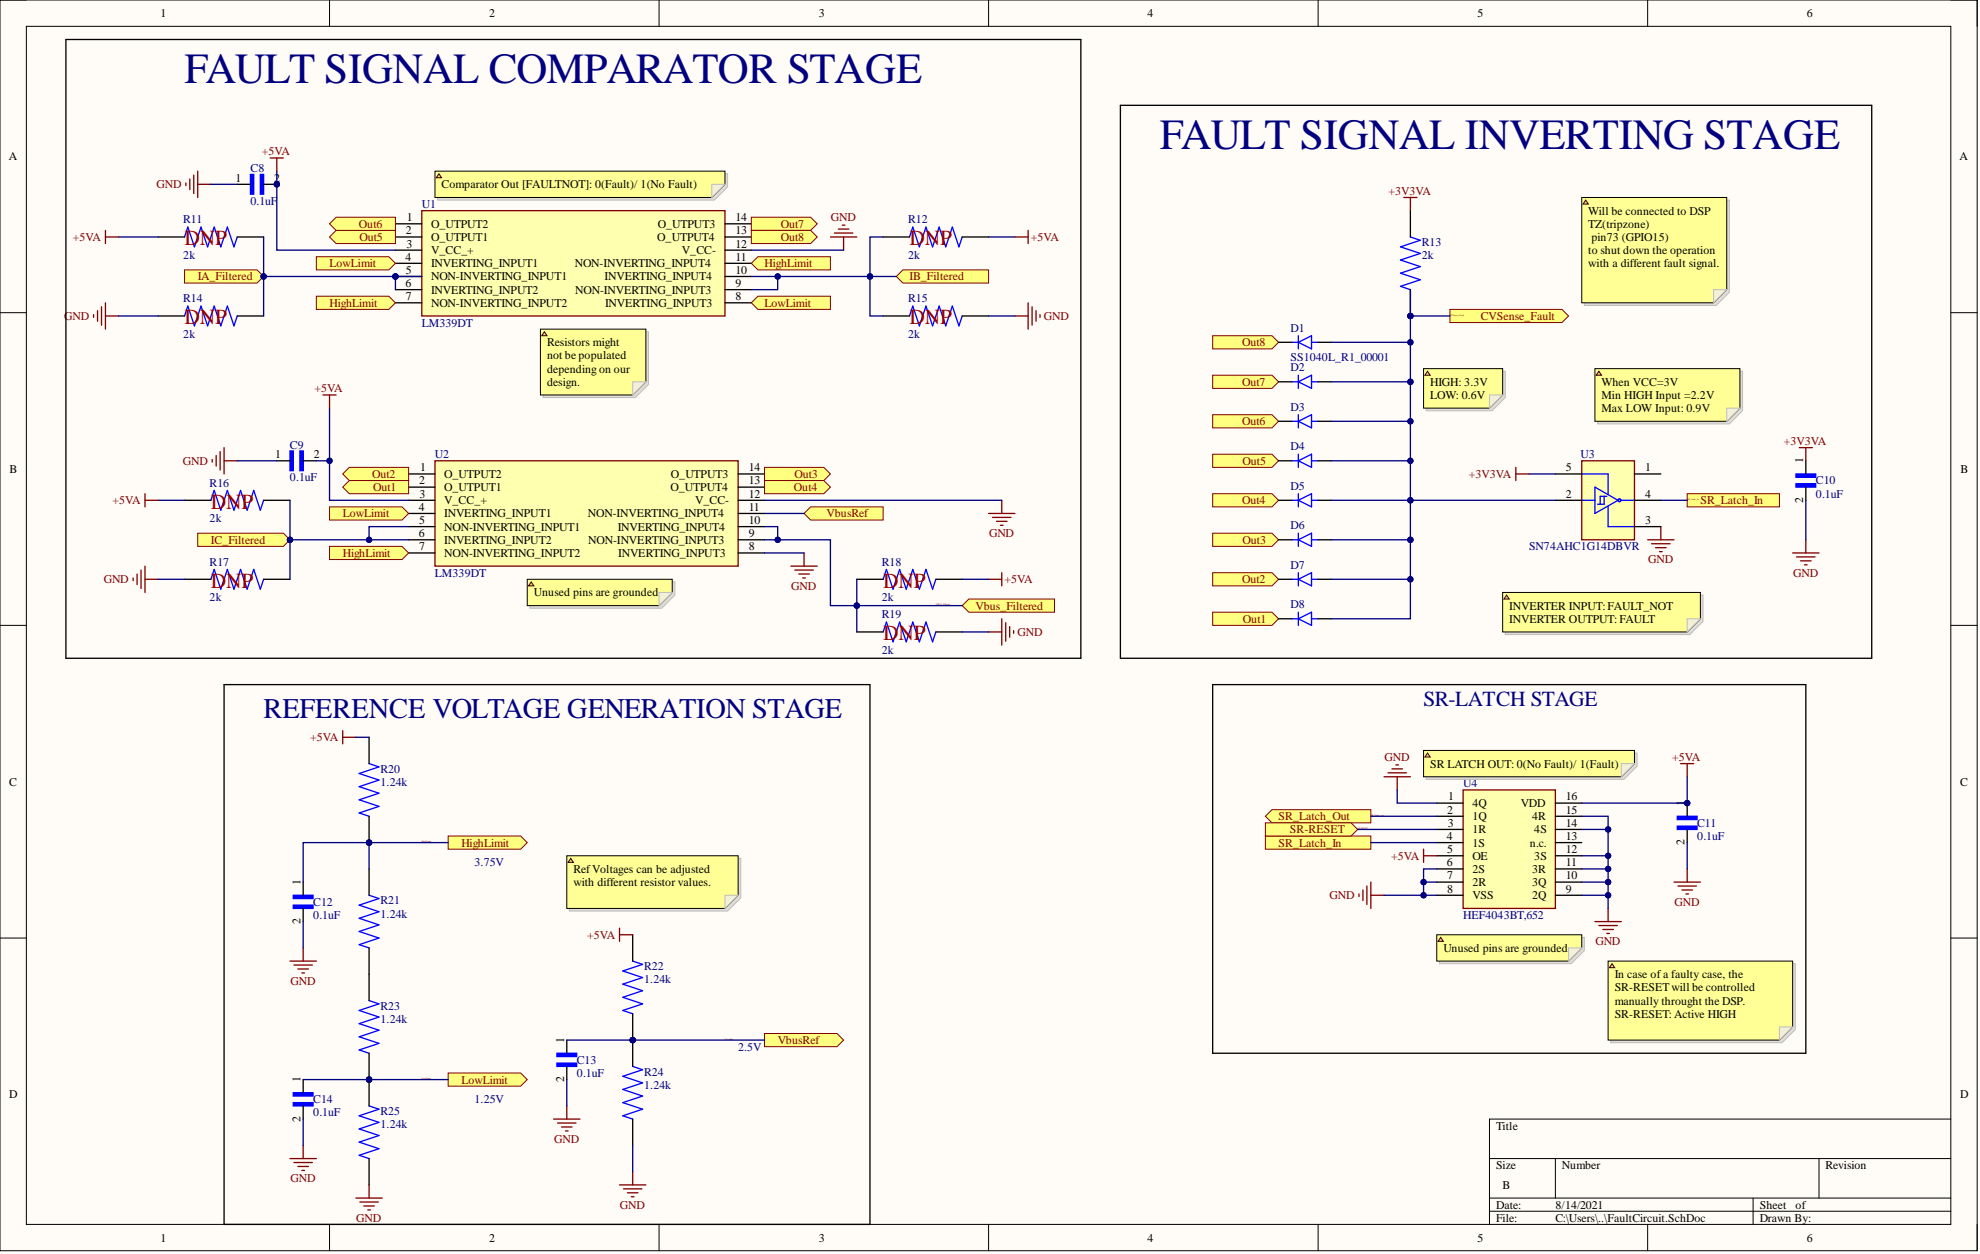
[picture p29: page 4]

FAULT SIGNAL COMPARATOR STAGE

FAULT SIGNAL INVERTING STAGE

Will be connected to DSP
TZ(tripzone)
pin73 (GPIO15)
to shut down the operation
with a different fault signal.

Unused pins are grounded

Ref Voltages can be adjusted
with different resistor values.

In case of a faulty case, the
SR-RESET will be controlled
manually throught the DSP.
SR-RESET: Active HIGH

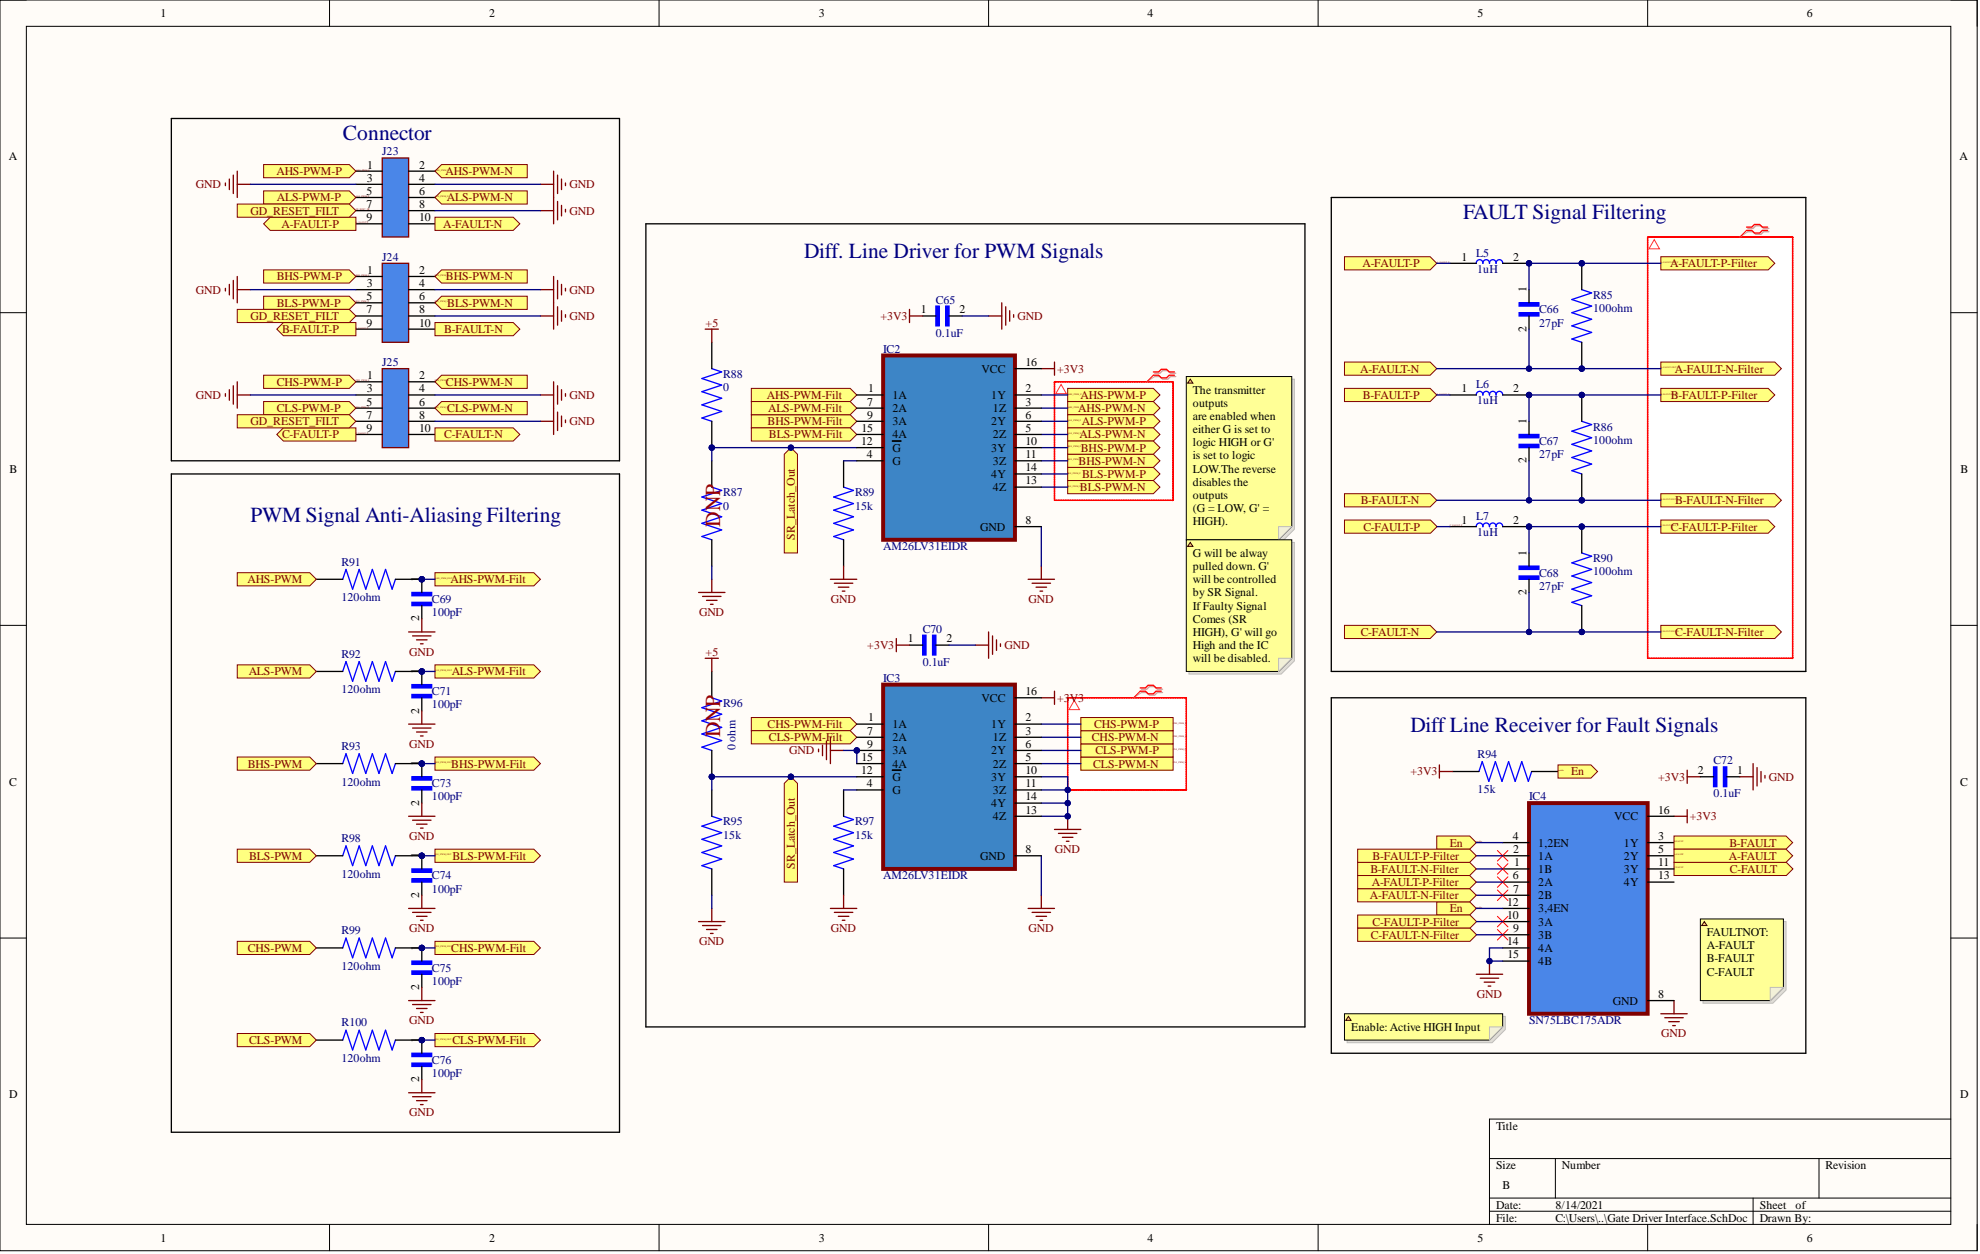
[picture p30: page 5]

HS-PWM-P ALS-PWM-P A-FAULT-P

Diff. Line Driver for PWM Sig

Diff Line Receiver for Fa

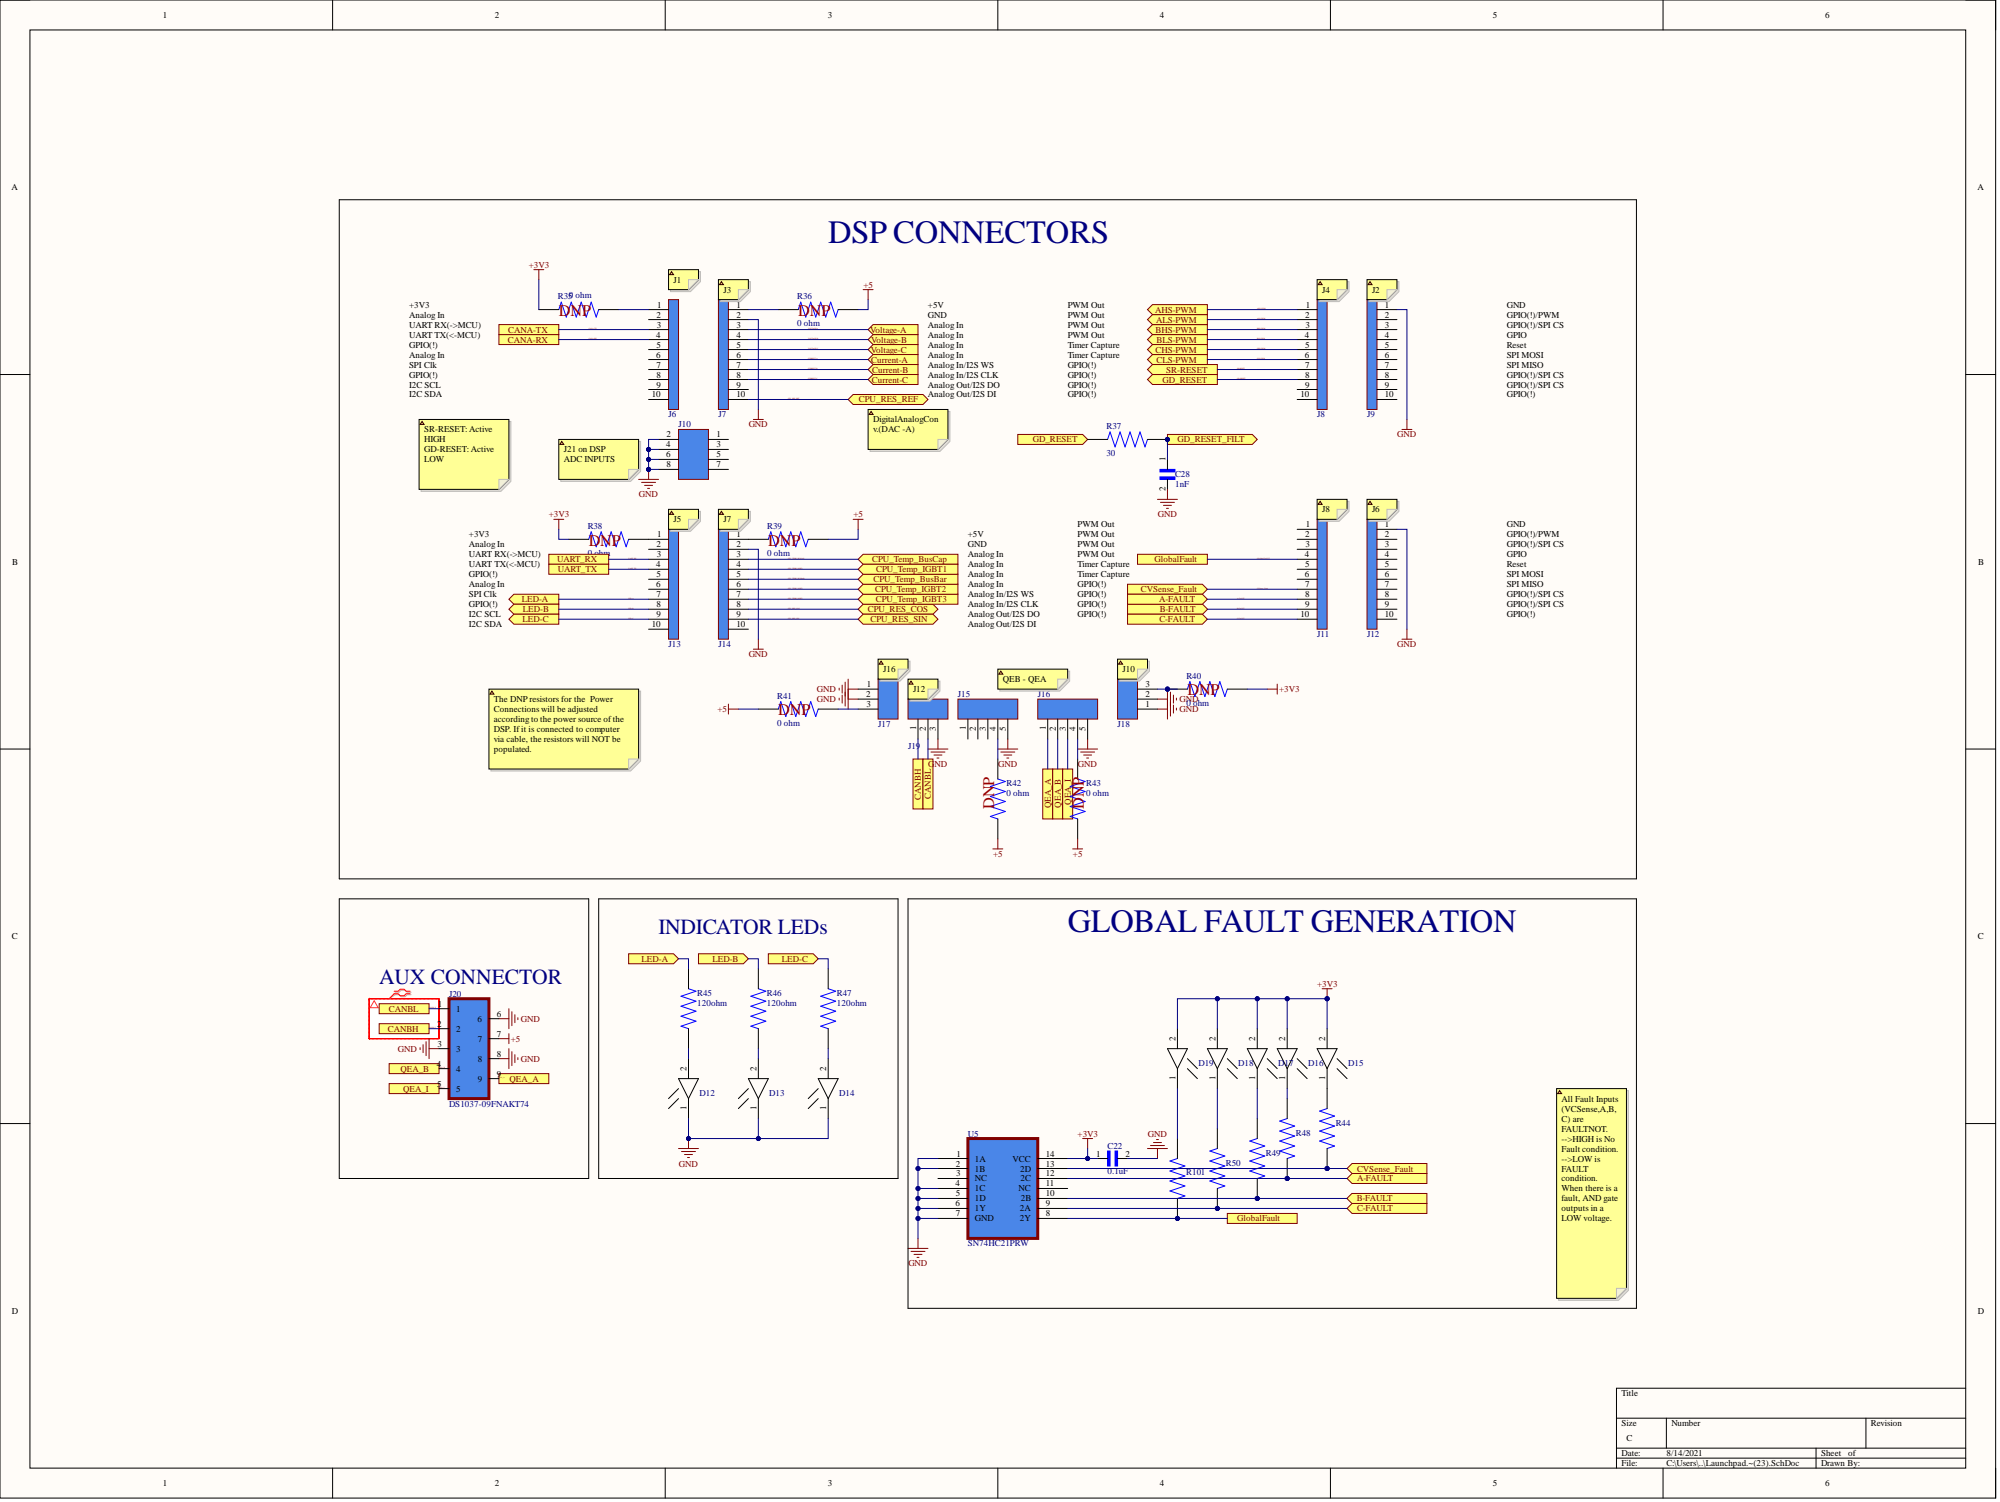
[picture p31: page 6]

The DNP resistors for the Power
Connections will be adjusted
according to the power source of the
DSP. If it is connected to computer
via cable, the resistors will NOT be
populated.

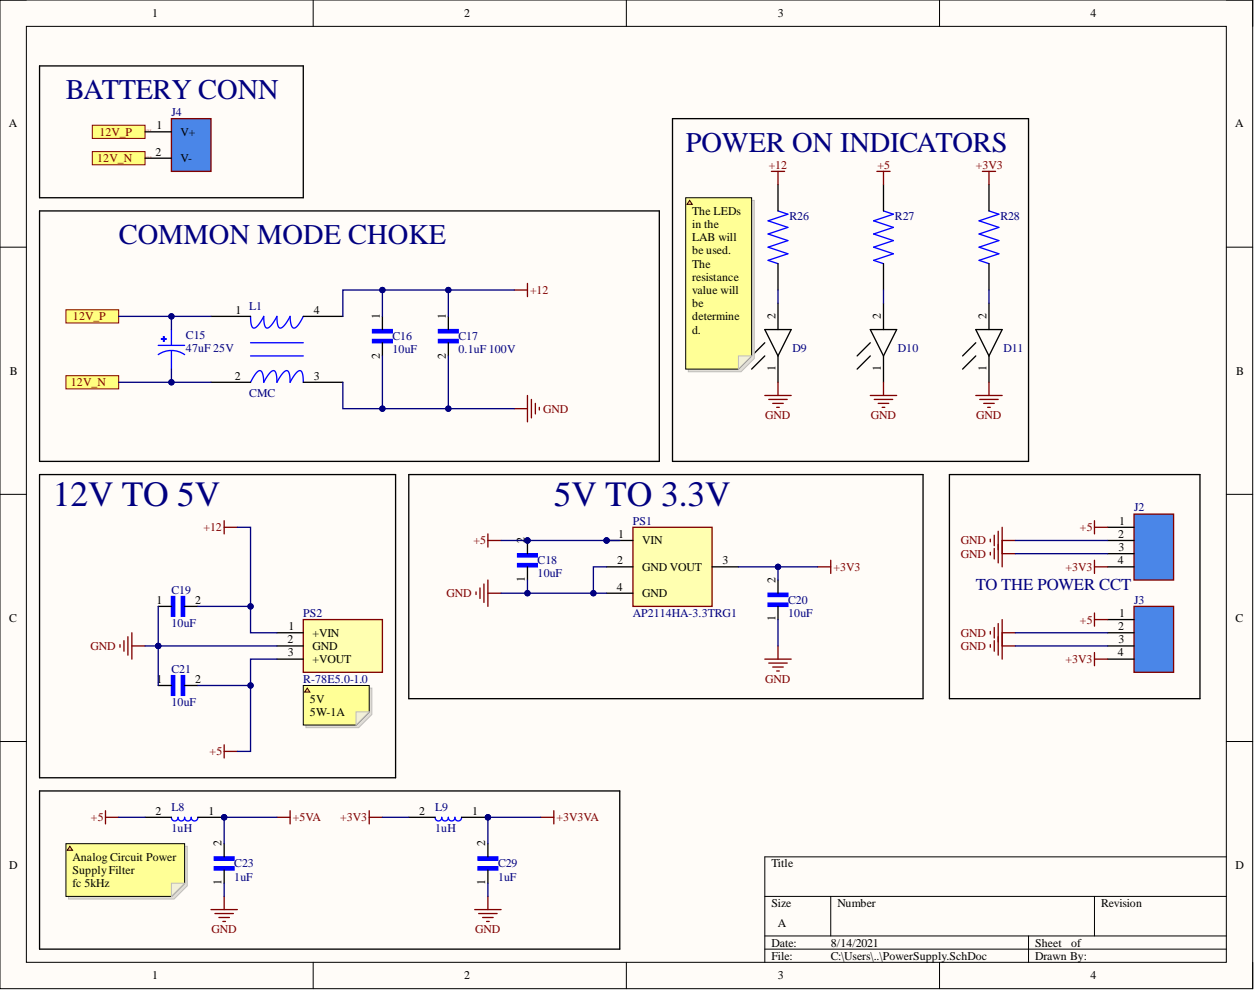
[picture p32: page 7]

GND
TO THE POWER CCT

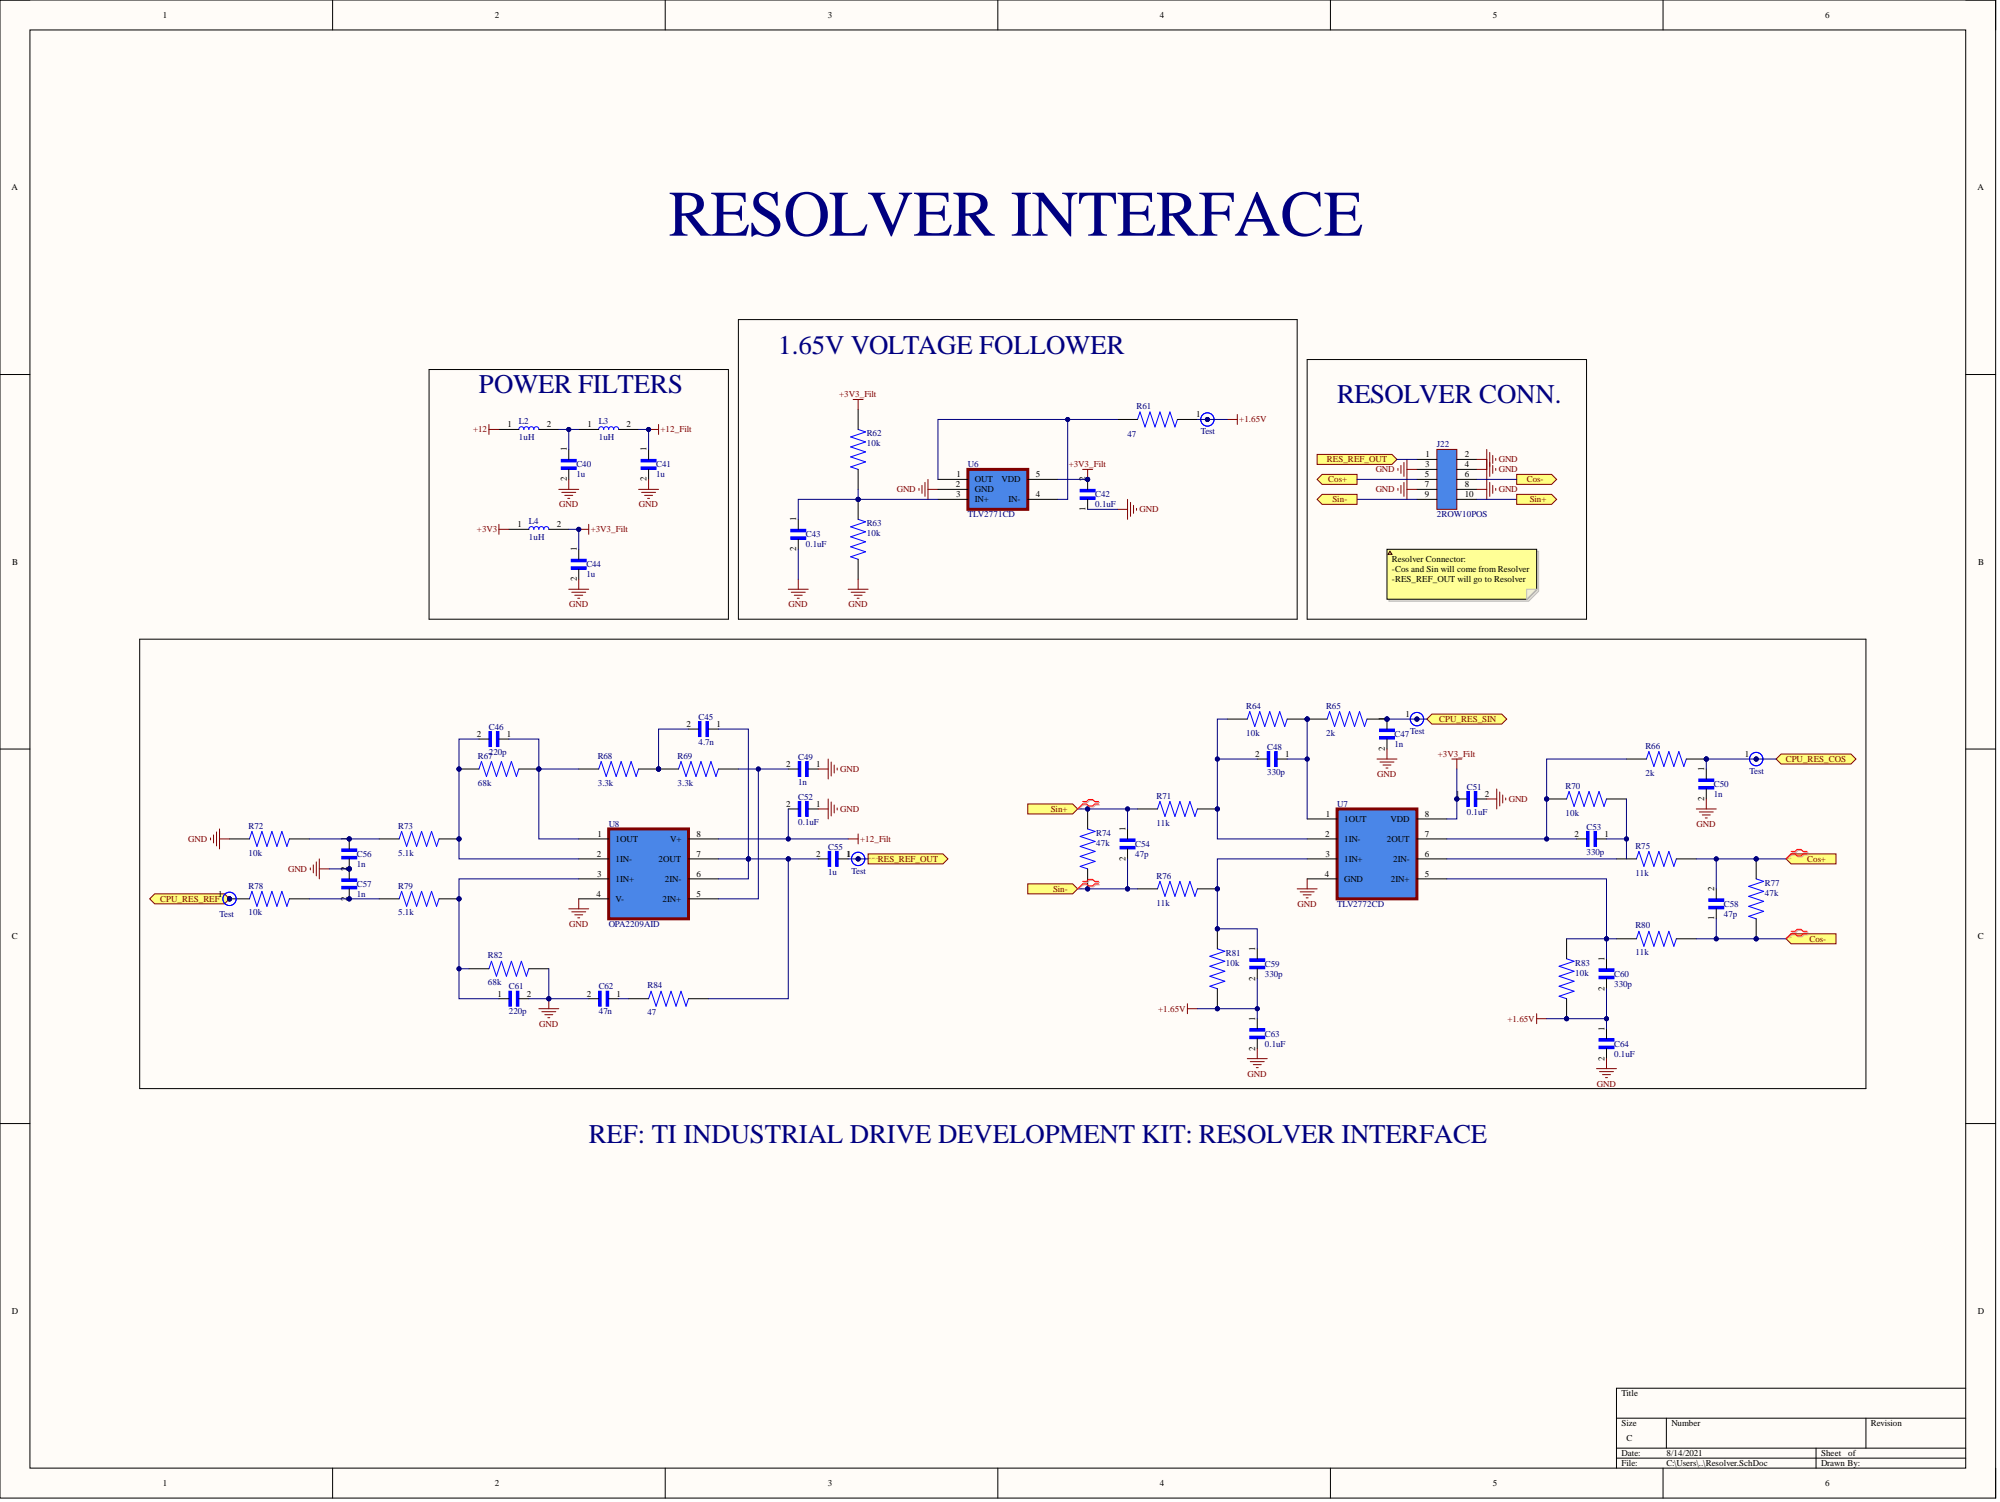
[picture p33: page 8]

Resolver Connector:
-Cos and Sin will come from Resolver
-RES_REF_OUT will go to Resolver

REF: TI INDUSTRIAL DRIVE DEVELOPMENT KIT: RESOLVER INTERFACE

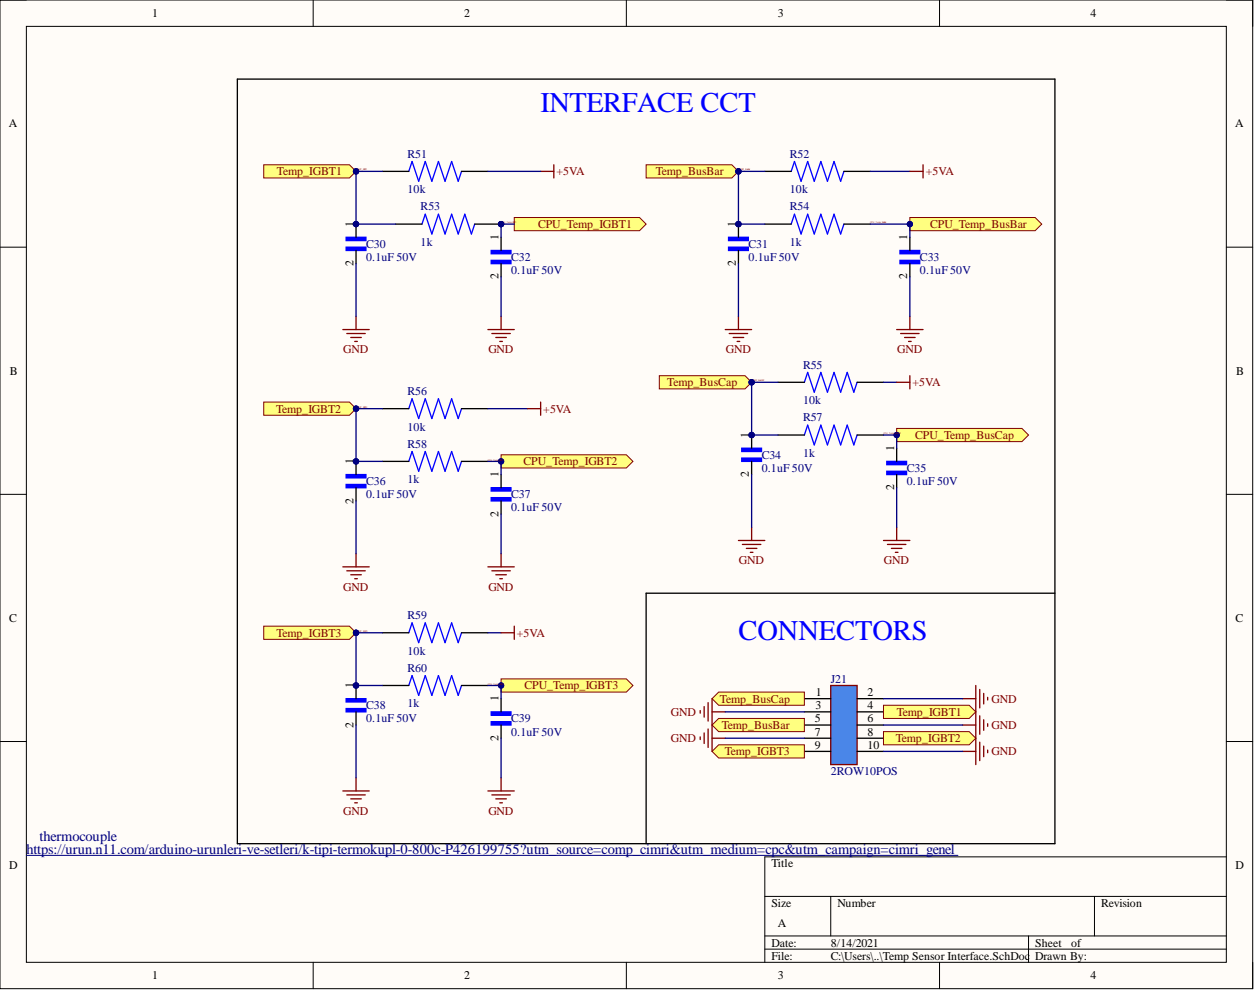
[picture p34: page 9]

thermocouple
https://urun.n11.com/arduino-urunleri-ve-setleri/k-tipi-termokupl-0-800c-P426199755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

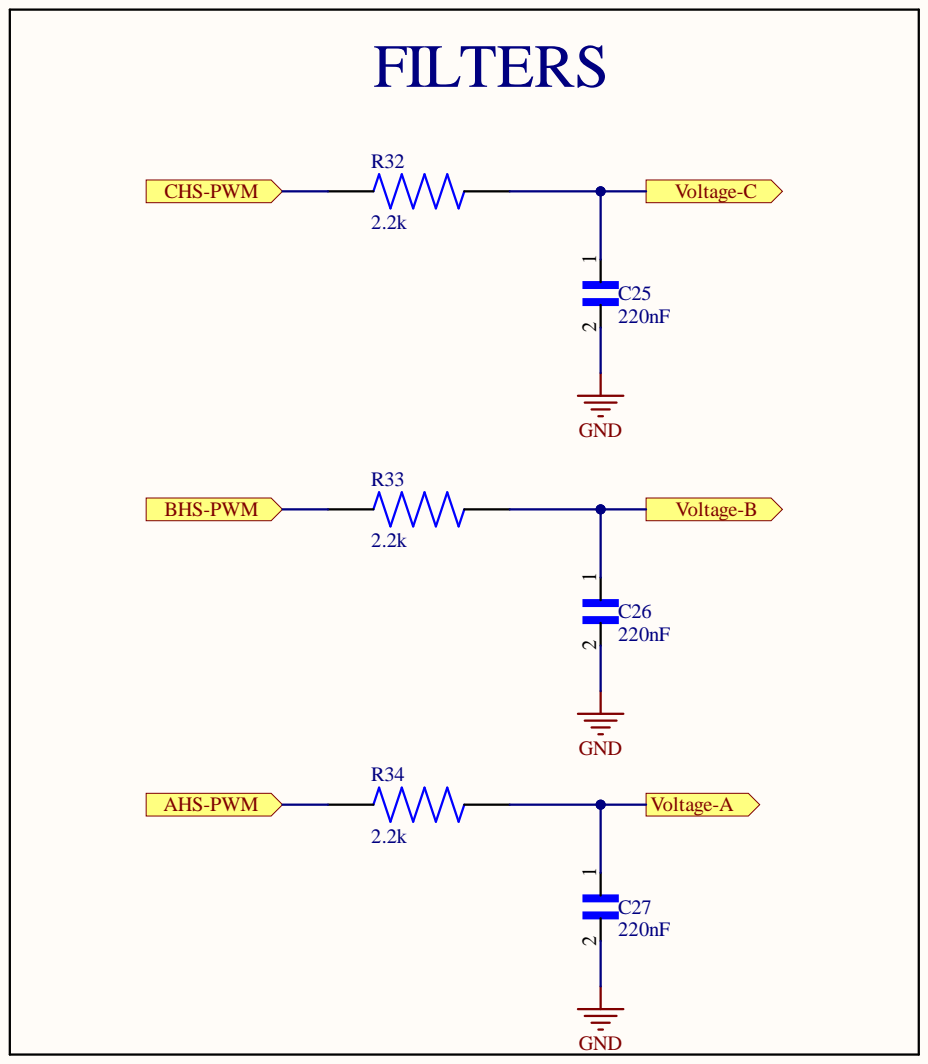
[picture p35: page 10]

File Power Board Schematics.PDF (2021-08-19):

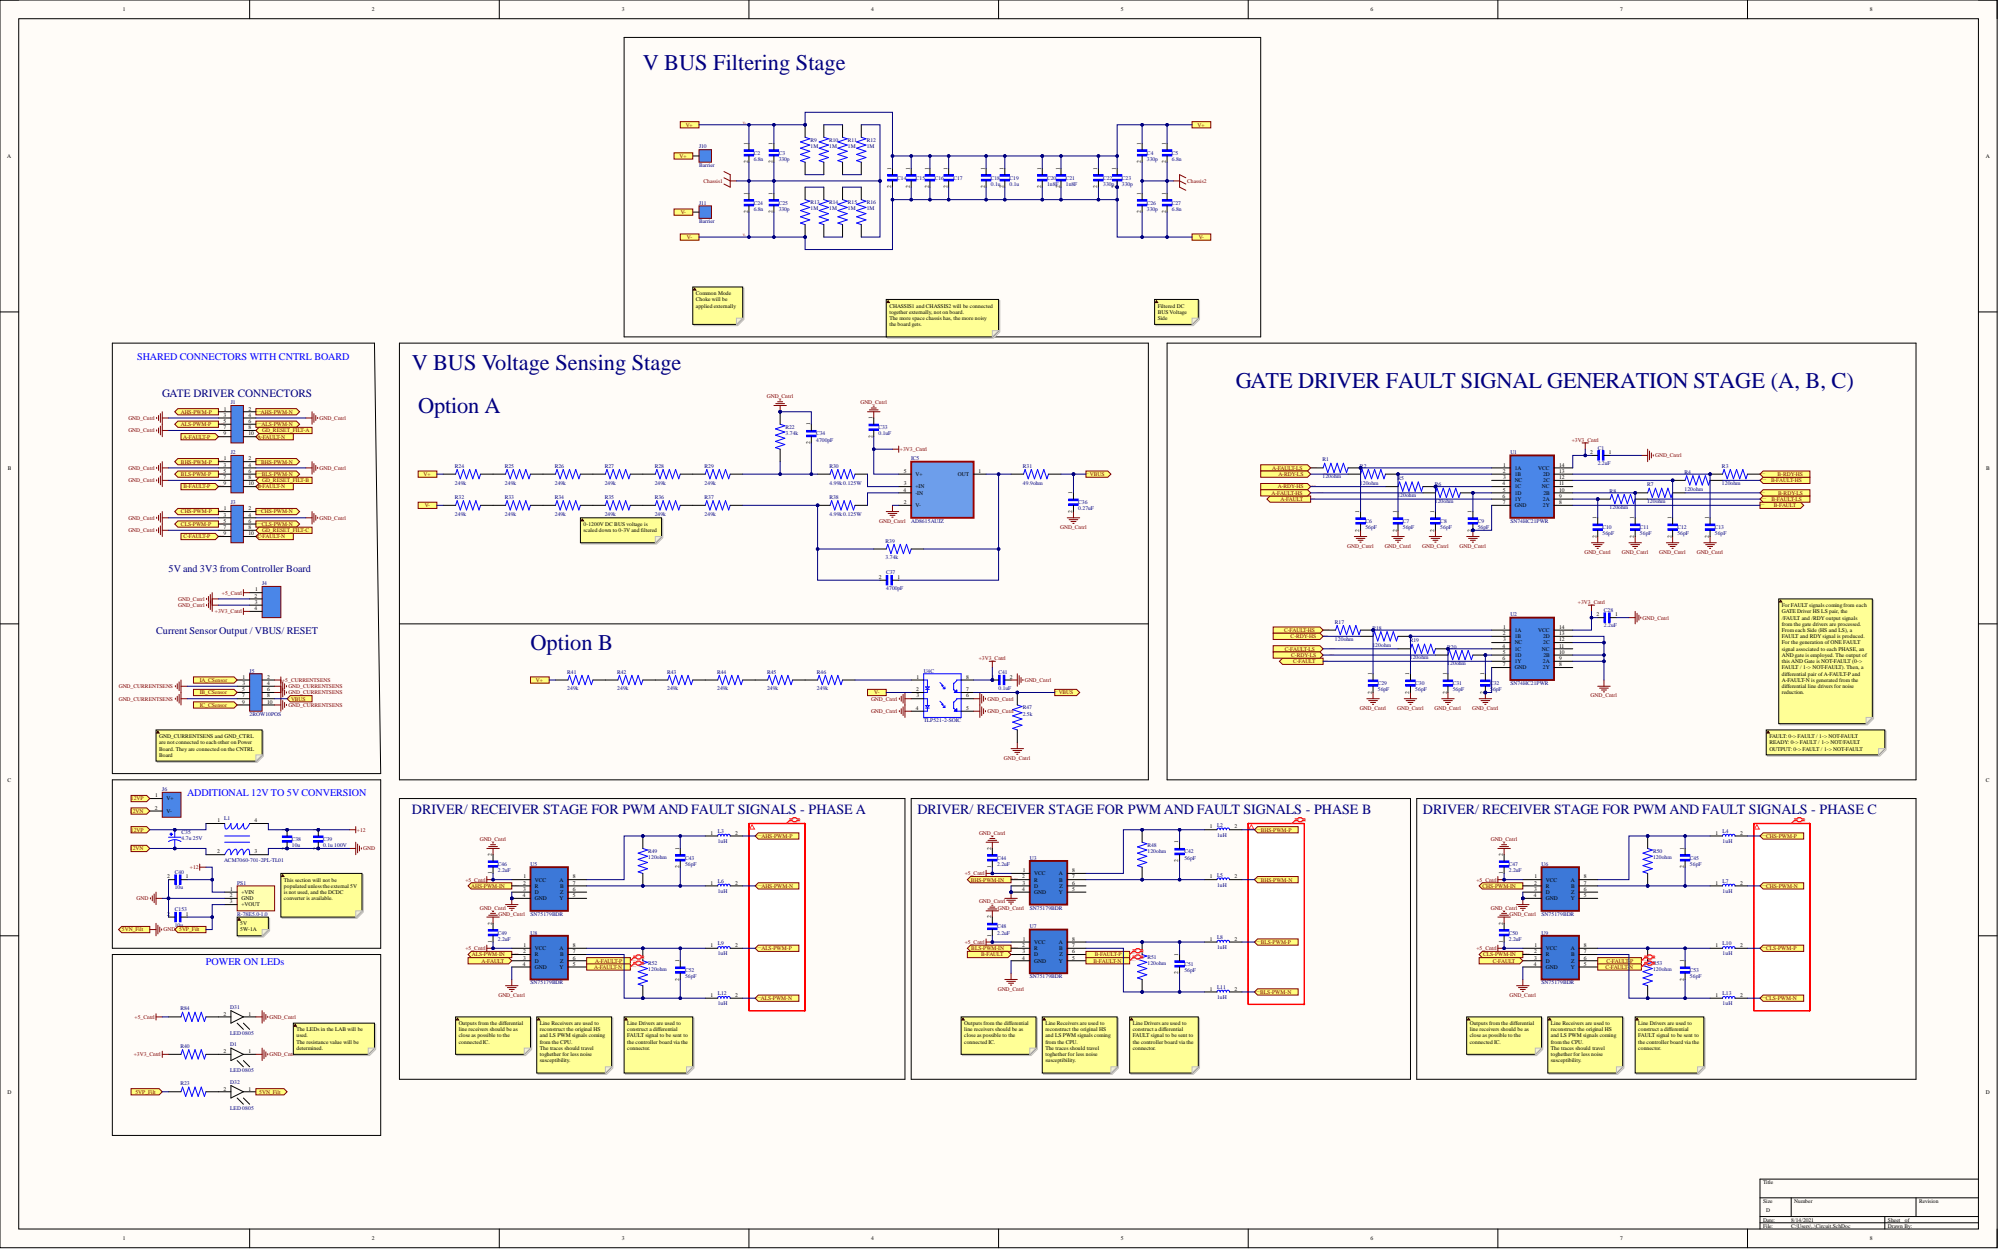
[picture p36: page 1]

CHASSIS1 and CHASSIS2 will be connected
together externally, not on board.
The more space chassis has, the more noisy
the board gets.

SHARED CONNECTORS WITH CNTRL BOARD

V BUS Voltage Sensing Stage

GATE DRIVER FAULT SIGNAL GENERATION STAGE (A, B, C)

B-RDY-HS
B-FAULT-HS

B-RDY-LS
B-FAULT-LS
B-FAULT

120ohm

0-1200V DC BUS voltage is
scaled down to 0-3V and filtered

5V and 3V3 from Controller Board

For FAULT signals coming from each
GATE Driver HS LS pair, the
/FAULT and /RDY output signals
from the gate drivers are processed.
From each Side (HS and LS), a
FAULT and RDY signal is produced.
For the generation of ONE FAULT
signal associated to each PHASE, an
AND gate is employed. The output of
this AND Gate is NOT-FAULT (0->
FAULT / 1-> NOT-FAULT). Then, a

Current Sensor Output / VBUS/ RESET

1D 5
1Y 6

differential pair of A-FAULT-P and
A-FAULT-N is generated from the
differential line drivers for noise
reduction.

GND_CURRENTSENS and GND_CTRL
are not connected to each other on Power
Board. They are connected on the CNTRL
Board

FAULT: 0-> FAULT / 1-> NOT-FAULT
READY: 0-> FAULT / 1-> NOT/FAULT
OUTPUT: 0-> FAULT / 1-> NOT-FAULT

DRIVER/ RECEIVER STAGE FOR PWM AND FAULT SIGNALS - PHASE A

This section will not be
populated unlessthe external 5V
is not used, and the DCDC
converter is available.

Outputs from the differential
line receivers should be as
close as possible to the
connected IC.

Line Receivers are used to
reconstruct the original HS
and LS PWM signals coming
from the CPU.
The traces should travel
toghether for less noise
susceptibility.

Line Drivers are used to
construct a differential
FAULT signal to be sent to
the controller board via the
connector.

The LEDs in the LAB will be
used.
The resistance value will be
determined.

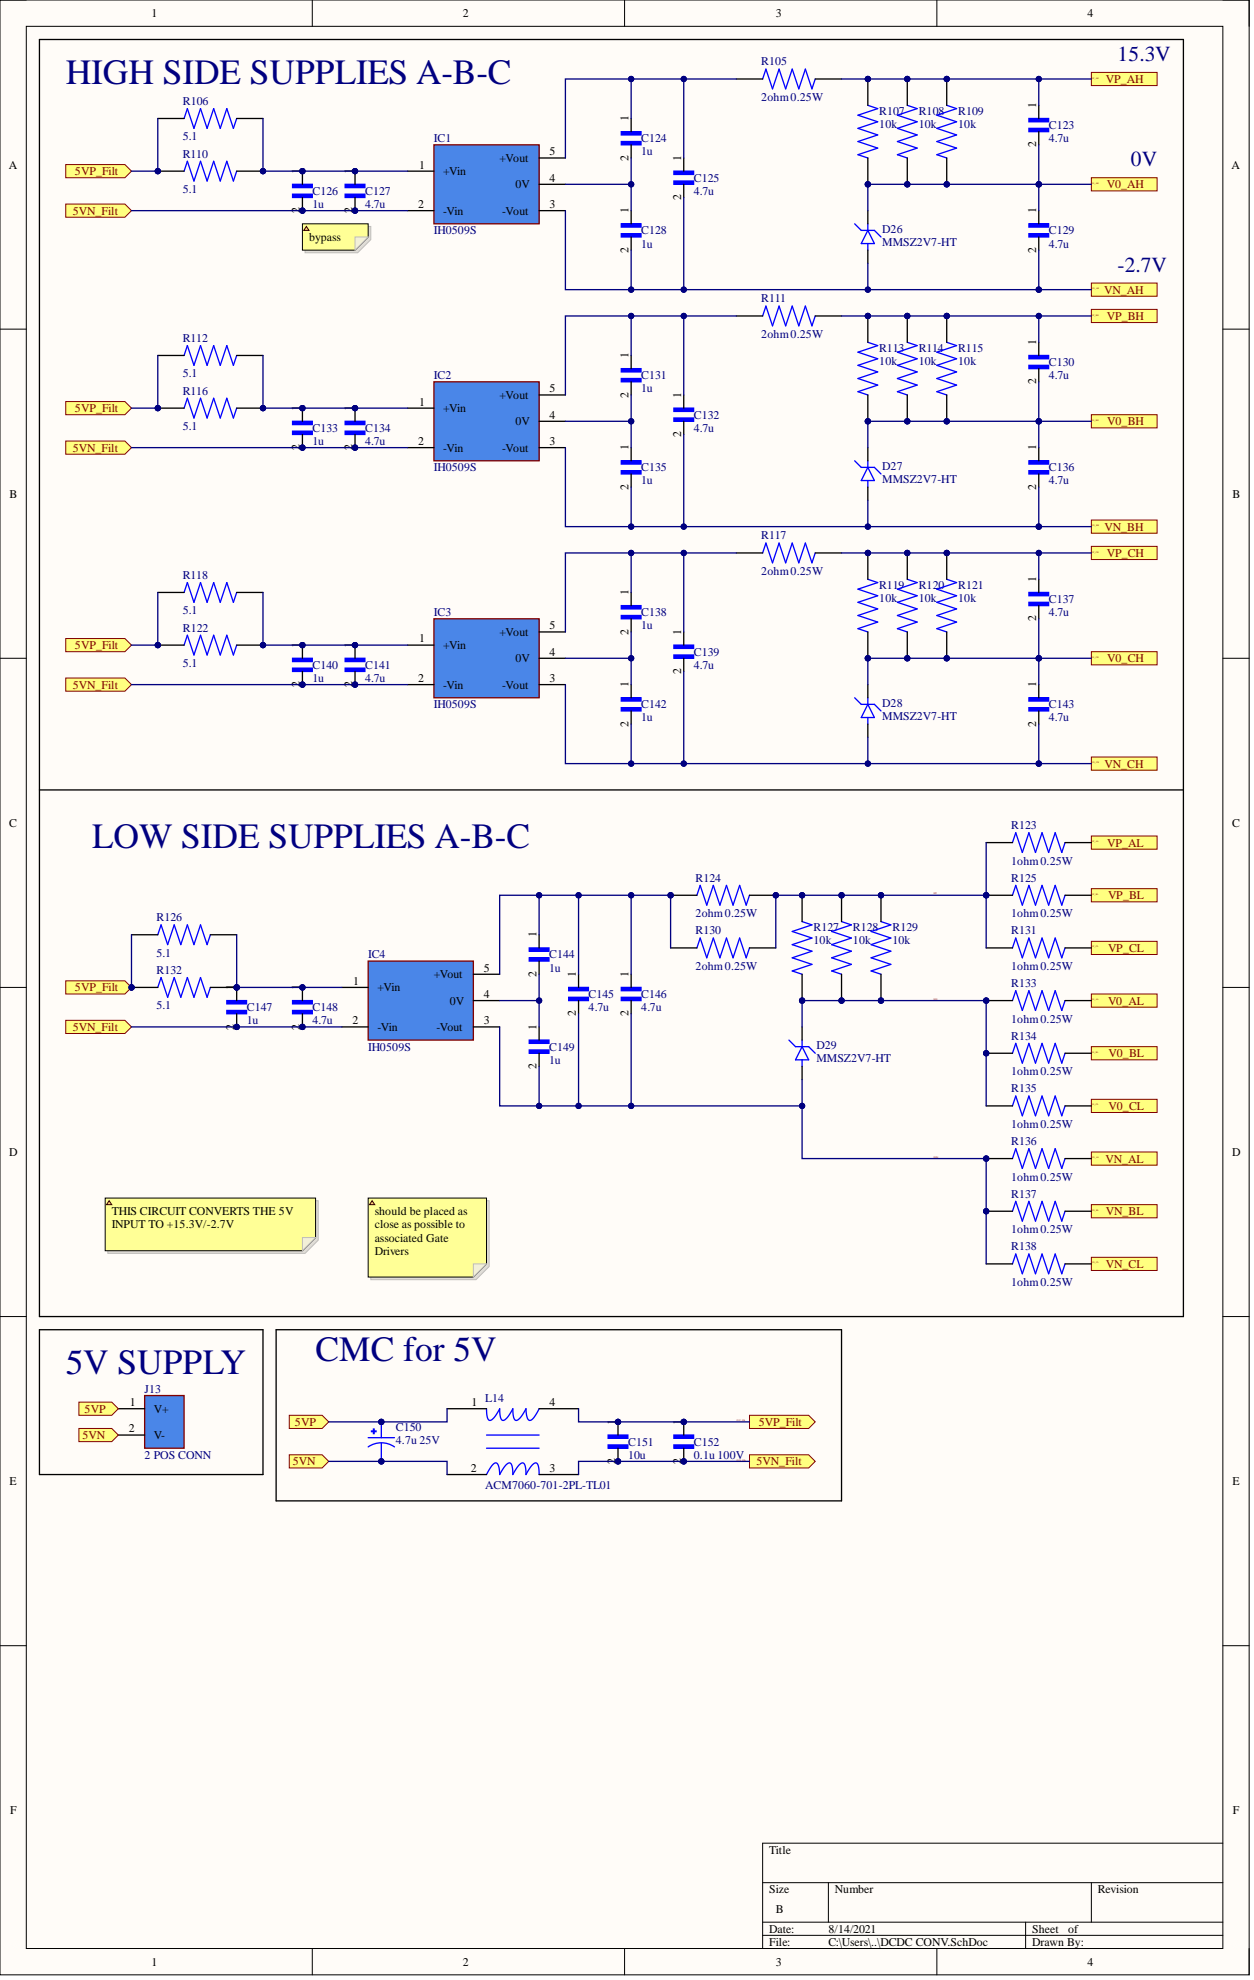
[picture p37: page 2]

THIS CIRCUIT CONVERTS THE 5V
INPUT TO +15.3V/-2.7V

should be placed as
close as possible to
associated Gate
Drivers


HIGH SIDE DRIVER- PHASE A

HIGH SIDE DRIVER- PHASE B

HIGH SIDE DRIVER- PHASE C

Gate Drive Current = 2A
DESAT: Desaturation protection
CLAMP: Miller clamping
RDY: Ready output
-Open-drain output to report the correct
operation of the device (RDY = high if both
chips are above the UVLO level and the
internal chip transmission is faultless).
/FLT: Fault Output, low active
-It is low in a fault case
/RST: Reset input, low active

LOW SIDE DRIVER- PHASE A

LOW SIDE DRIVER- PHASE B

LOW SIDE DRIVER- PHASE C

Q13 | Q14 Q15
DRAIN_BH | | DRAIN_CH Q16

10ohm0.5W S IXFH42N60P3 | 10ohm0.5W S

3 | 3 | GATE_CL

IXFH42N60P3 | IXFH42N60P3

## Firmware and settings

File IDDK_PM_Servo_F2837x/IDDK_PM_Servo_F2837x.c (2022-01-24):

/* ============================================================================
System Name:  	IDDK Sevo Control

File Name:	  	IDDK_Servo.C

Target:			Rev 1.1 of the F2837x control card

Author:			C2000 Systems Lab, 05th March 2015

Description:	Project uses two ISRs
				1. Resolver ISR triggered by ADC INT, this is defined as the
				     high priority interrupt and runs at 160Khz
				2. Inverter ISR rate is 10Khz and is triggered by EPM11,
				     reason to choose EPWM11 is because of the SD reading
				     EPWM11 provides periodic sync resets to the SDFM module,
				     after each reset the SDFM data is ready after 3 OSRs and
				     needs to be read immediately.

Peripheral functions:
   EPWMs
		- EPWM1, EPWM2, EPWM3 ---> Inverter PWMs for phases A, B, C
		- EPWM5  ---> clk for Sigma Delta
		- EPWM6  ---> Resolver feedback sampling @ 160KHz
		- EPWM11 ---> sync SD filter windows with motor control PWMs

	Analog to Digital Conversion channels
	  ADC A4/C+  --->  Ifb-SV
	  ADC B4/C+  ---> Ifb-SW
	  ADC A2/C+  ---> LEM V
	  ADC B2/C+  ---> LEM W
	  ADC D1     ---> R_SIN
	  ADC C1     ---> R_COS

	 Analog Signals brought in but not sampled
	  ADC C2/C+  ---> Ifb-SU
	  ADC A5     --->
	  ADC C3     ---> Vfb-U
	  ADC A3     ---> Vfb-V
	  ADC B3     ---> Vfb-W
	  ADC B0     ---> Vfb-Bus
	  ADC C0/C+  ---> SC-A2
	  ADC D0/C+  ---> SC-B2
	  ADC D2/C+  ---> SC-R

	  DAC-A  ---> Resolver carrier excitation
	  DAC-B  ---> General purpose display
	  DAC-C  ---> General purpose display

===========================================================================  */

// Include header files used in the main function
// define float maths and then include IQmath library

#include "IDDK_PM_Servo_F2837x-Settings.h"

#ifdef FLASH
#pragma CODE_SECTION(MotorControlISR,"ramfuncs");
#pragma CODE_SECTION(ResolverISR,"ramfuncs");
#endif

#pragma INTERRUPT (ResolverISR, HPI)
#pragma INTERRUPT (MotorControlISR, LPI)

// Prototype statements for functions found within this file.
interrupt void MotorControlISR(void);
interrupt void ResolverISR(void);
void DeviceInit();
void MemCopy();
void InitFlash();
void HVDMC_Protection(void);
void PWM_1ch_UpDwnCnt_CNF(int16 n, Uint16 period, int16 db);
void PWM_1ch_UpCnt_CNF(int16 n, Uint16 period);
void ConfigureADC(void);

// **********************************************************
// ********************* Functions **************************
// **********************************************************
_iq refPosGen(_iq out);
_iq ramper(_iq in, _iq out, _iq rampDelta);

// State Machine function prototypes
//------------------------------------
// Alpha states
void A0(void);	//state A0
void B0(void);	//state B0
void C0(void);	//state C0

// A branch states
void A1(void);	//state A1
void A2(void);	//state A2
void A3(void);	//state A3

// B branch states
void B1(void);	//state B1
void B2(void);	//state B2
void B3(void);	//state B3

// C branch states
void C1(void);	//state C1
void C2(void);	//state C2
void C3(void);	//state C3

// Variable declarations
void (*Alpha_State_Ptr)(void);	// Base States pointer
void (*A_Task_Ptr)(void);		// State pointer A branch
void (*B_Task_Ptr)(void);		// State pointer B branch
void (*C_Task_Ptr)(void);		// State pointer C branch

// ****************************************************************************
// Variables for CPU control
// ****************************************************************************
// adc static cal
int *adc_cal;

// Used to indirectly access all EPWM modules
volatile struct EPWM_REGS *ePWM[] = {
		&EPwm1Regs,			//intentional: (ePWM[0] not used)
		&EPwm1Regs, &EPwm2Regs, &EPwm3Regs, &EPwm4Regs, &EPwm5Regs, &EPwm6Regs,
		&EPwm7Regs, &EPwm8Regs, &EPwm9Regs, &EPwm10Regs, &EPwm11Regs, &EPwm12Regs};

volatile struct SDFM_REGS *SDFM[] =
{	0, &Sdfm1Regs, &Sdfm2Regs};

// Used to indirectly access eQEP module
volatile struct EQEP_REGS *eQEP[] =
 				  { &EQep1Regs,
 				  	&EQep1Regs,
					&EQep2Regs,
				  };

int16	VTimer0[4];			// Virtual Timers slaved off CPU Timer 0 (A events)
int16	VTimer1[4]; 		// Virtual Timers slaved off CPU Timer 1 (B events)
int16	VTimer2[4]; 		// Virtual Timers slaved off CPU Timer 2 (C events)
int16	SerialCommsTimer;

// Default ADC initialization
int ChSel[16]   = {0,0,0,0,0,0,0,0,0,0,0,0,0,0,0,0};
int	TrigSel[16] = {5,5,5,5,5,5,5,5,5,5,5,5,5,5,5,5};
int ACQPS[16]   = {8,8,8,8,8,8,8,8,8,8,8,8,8,8,8,8};

//*********************** USER Variables *************************************
// Global variables used in this system
//****************************************************************************

// ****************************************************************************
// Variables for current measurement
// ****************************************************************************
// Offset calibration routine is run to calibrate for any offsets on the opamps
_iq offset_shntV,        // offset in shunt current V fbk channel @ 0A
    offset_shntW,        // offset in shunt current W fbk channel @ 0A
	offset_shntU,        // offset in shunt current U fbk channel @ 0A
    offset_Rsin,         // offset in resolver sine fbk channel @ no excitation
	offset_Rcos,         // offset in resolver cos  fbk channel @ no excitation
	offset_lemV,         // offset in LEM current V fbk channel @ 0A
	offset_lemW;         // offset in LEM current W fbk channel @ 0A

int16 OffsetCalCounter;

//SD Trip Level - scope for additonal work
Uint16  HLT = 0x7FFF,
        LLT = 0x0;

volatile float offset_SDFM1;  // offset in SD current V fbk channel @ 0A
volatile float offset_SDFM2;  // offset in SD current W fbk channel @ 0A

_iq K1 = _IQ(0.998),		  // Offset filter coefficient K1: 0.05/(T+0.05);
    K2 = _IQ(0.001999);	      // Offset filter coefficient K2: T/(T+0.05);

typedef struct {
	float As;      // phase A
	float Bs;      // phase B
	float Cs;      // phase C
} CURRENT_SENSOR;

CURRENT_SENSOR current_sensor[3];

// ****************************************************************************
// Flag variables
// ****************************************************************************
volatile Uint16 EnableFlag = FALSE;

Uint32 IsrTicker = 0;

Uint16 BackTicker = 0,
       lsw = 0,
       TripFlagDMC = 0,				//PWM trip status
       clearTripFlagDMC = 0,
       RunMotor = 0;

int    EnableResolverISR,  // not used
       Run_Delay,          // not used
       LedCnt1=0;

Uint16 SpeedLoopPrescaler = 10,      // Speed loop pre scalar
       SpeedLoopCount = 1;           // Speed loop counter

// ****************************************************************************
// Variables for Field Oriented Control
// ****************************************************************************
float32 T = 0.001/ISR_FREQUENCY;    // Samping period (sec), see parameter.h
_iq VdTesting = _IQ(0.0),			// Vd reference (pu)
    VqTesting = _IQ(0.10),			// Vq reference (pu)
    IdRef     = _IQ(0.0),			// Id reference (pu)
    IqRef     = _IQ(0.0),			// Iq reference (pu)
    SpeedRef  = _IQ(0.0);           // For Closed Loop tests

// Instance a few transform objects
CLARKE clarke1 = CLARKE_DEFAULTS;
PARK   park1   = PARK_DEFAULTS;
IPARK  ipark1  = IPARK_DEFAULTS;

// Instance PI(D) regulators to regulate the d and q  axis currents, speed and position
PIDREG3         pid_pos = PIDREG3_DEFAULTS;          // (optional - for eval)
PI_CONTROLLER   pi_pos  = PI_CONTROLLER_DEFAULTS;
PID_CONTROLLER	pid_spd = {PID_TERM_DEFAULTS, PID_PARAM_DEFAULTS, PID_DATA_DEFAULTS};
PI_CONTROLLER   pi_id   = PI_CONTROLLER_DEFAULTS;
PI_CONTROLLER   pi_iq   = PI_CONTROLLER_DEFAULTS;

//PID_CONTROLLER	pid_pos = {PID_TERM_DEFAULTS, PID_PARAM_DEFAULTS, PID_DATA_DEFAULTS};
//PI_CONTROLLER pi_spd = PI_CONTROLLER_DEFAULTS;

// Instance a PWM driver instance
//PWMGEN pwm1 = PWMGEN_DEFAULTS;

// Instance a Space Vector PWM modulator. This modulator generates a, b and c
// phases based on the d and q stationery reference frame inputs
SVGEN svgen1 = SVGEN_DEFAULTS;

// Instance a ramp controller to smoothly ramp the frequency
RMPCNTL rc1 = RMPCNTL_DEFAULTS;
RMPCNTL rc2 = RMPCNTL_DEFAULTS; // for speed

//	Instance a ramp generator to simulate an Anglele
RAMPGEN rg1 = RAMPGEN_DEFAULTS;

//	Instance a phase voltage calculation
PHASEVOLTAGE volt1 = PHASEVOLTAGE_DEFAULTS;

// Instance a speed calculator based on Encoder position
SPEED_MEAS_QEP speed1 = SPEED_MEAS_QEP_DEFAULTS;

// Instance a QEP interface driver
QEP qep1 = QEP_DEFAULTS;

// Instance a RESOLVER interface driver
volatile RESOLVER resolver1 = RESOLVER_DEFAULTS;

// Variables for Position Sensor Suite
_iq posEncElecTheta[6],
    posEncMechTheta[6];

_iq  cntr=0,
	 alignCnt = 20000;
_iq  IdRef_start = _IQ(0.1),
	 IdRef_run   = _IQ(0.0);

// Variables for position reference generation and control
// =========================================================
_iq   posArray[8] = { _IQ(1.5), _IQ(-1.5), _IQ(2.5), _IQ(-2.5) },
	  cntr1=0 ,
	  posSlewRate = _IQ(0.001);

int16 ptrMax = 2,
      ptr1=0;

// ****************************************************************************
// Extern functions and variables referred from resolver.c
// ****************************************************************************
extern void baseParamsInit(void);
extern void derivParamsCal(void);

extern RESOLVER_OUTPUT rslvrOut;

// ****************************************************************************
// Variables for Datalog module
// ****************************************************************************
float DBUFF_4CH1[200],
      DBUFF_4CH2[200],
      DBUFF_4CH3[200],
      DBUFF_4CH4[200],
      DlogCh1,
      DlogCh2,
      DlogCh3,
      DlogCh4;

// Create an instance of DATALOG Module
DLOG_4CH_F dlog_4ch1;

//*******************************************************************************

// ******************************************************************************
// CURRENT SENSOR SUITE
// - Reads motor current from inverter bottom leg SHUNT
// - Reads motor current from LEM flux gate current sensors connected to motor
//     phases V and W
// - Reads motor current from series shunt connected to motor using isolated
//     Sigma Delta Filter Module
// ******************************************************************************
#if BUILDLEVEL != LEVEL1
inline void currentSensorSuite()
{
	volatile int16 temp;  // temp variable used to avoid warning msgs

	current_sensor[SHUNT_CURRENT_SENSE-1].As = (float)IFB_SV_PPB* ADC_PU_PPB_SCALE_FACTOR;
	current_sensor[SHUNT_CURRENT_SENSE-1].Bs = (float)IFB_SW_PPB* ADC_PU_PPB_SCALE_FACTOR;
	current_sensor[SHUNT_CURRENT_SENSE-1].Cs = -current_sensor[SHUNT_CURRENT_SENSE-1].Cs
			                                   -current_sensor[SHUNT_CURRENT_SENSE-1].Bs;

	current_sensor[LEM_CURRENT_SENSE-1].As   = (float)IFB_LEMV_PPB* ADC_PU_PPB_SCALE_FACTOR * LEM_TO_SHUNT;
	current_sensor[LEM_CURRENT_SENSE-1].Bs   = (float)IFB_LEMW_PPB* ADC_PU_PPB_SCALE_FACTOR * LEM_TO_SHUNT;
	current_sensor[LEM_CURRENT_SENSE-1].Cs   = -current_sensor[LEM_CURRENT_SENSE-1].Cs
			                                   -current_sensor[LEM_CURRENT_SENSE-1].Bs;

	current_sensor[SD_CURRENT_SENSE-1].As    = ((temp=SDFM1_READ_FILTER1_DATA_16BIT)*SD_PU_SCALE_FACTOR -
			                                    offset_SDFM1) * SDFM_TO_SHUNT;
	current_sensor[SD_CURRENT_SENSE-1].Bs    = ((temp=SDFM1_READ_FILTER2_DATA_16BIT)*SD_PU_SCALE_FACTOR -
			                                    offset_SDFM2) * SDFM_TO_SHUNT;
	current_sensor[SD_CURRENT_SENSE-1].Cs    = -current_sensor[SD_CURRENT_SENSE-1].Cs
			                                   -current_sensor[SD_CURRENT_SENSE-1].Bs;

	return;
}
#endif

// ******************************************************************************
// POSITION ENCODER SUITE
// - Reads QEP
// - Decodes RESOLVER (core algo is available in resolver.lib)
// - Angles are normalised to the the range 0 to 0.99999 (1.0)
// ******************************************************************************
void posEncoderSuite(void)
{
// ----------------------------------
// lsw = 0 ---> Alignment Routine
// ----------------------------------
#if (POSITION_ENCODER == QEP_POS_ENCODER)
	if (lsw == 0)
	{
		// during alignment, assign the current shaft position as initial position
		EQep1Regs.QPOSCNT = 0;
		EQep1Regs.QCLR.bit.IEL = 1;  // Reset position cnt for QEP
	} // end if (lsw=0)

// ******************************************************************************
//    Detect calibration angle and call the QEP module
// ******************************************************************************
	// for once the QEP index pulse is found, go to lsw=2
	if(lsw==1)
	{
		if (EQep1Regs.QFLG.bit.IEL == 1)			// Check the index occurrence
		{
			qep1.CalibratedAngle=EQep1Regs.QPOSILAT;
//			EQep1Regs.QPOSINIT = EQep1Regs.QPOSILAT; //new
//			EQep1Regs.QEPCTL.bit.IEI = IEI_RISING;   // new
			lsw=2;
		}   // Keep the latched pos. at the first index
	}

	if (lsw!=0){
		QEP_MACRO(1,qep1);
	}

	// Reverse the sense of position if needed - comment / uncomment accordingly
	// Position Sense as is
	//posEncElecTheta[QEP_POS_ENCODER] = qep1.ElecTheta;
	//posEncMechTheta[QEP_POS_ENCODER] = qep1.MechTheta;

	// Position Sense Reversal
	posEncElecTheta[QEP_POS_ENCODER] = 1.0 - qep1.ElecTheta;
	posEncMechTheta[QEP_POS_ENCODER] = 1.0 - qep1.MechTheta;

// ******************************************************************************
//  Read resolver data, get position and speed feedback
// ******************************************************************************
#elif (POSITION_ENCODER == RESOLVER_POS_ENCODER)
	// during alignment, assign the current shaft position as initial position
	if (lsw == 0)
	{
		resolver1.InitTheta = resolver1.RawTheta;
	}

	resolver1.Speed    = rslvrOut.angleObs;
	resolver1.RawTheta = (rslvrOut.angleObs*0.5)+0.5;
	//RESOLVER_MACRO_F(resolver1)
	resolver1.MechTheta   = resolver1.RawTheta - resolver1.InitTheta;      /* MechTheta in step counts */
	if(resolver1.MechTheta < 0)
		resolver1.MechTheta = resolver1.MechTheta + 1.0;
	else if (resolver1.MechTheta > 1.0)
		resolver1.MechTheta = resolver1.MechTheta - 1.0;

    // Compute the electrical angle in Q24
	resolver1.ElecTheta  = _IQfrac(resolver1.PolePairs * resolver1.MechTheta);

	// Reverse the sense of position if needed - comment / uncomment accordingly
	// Position Sense as is
	posEncElecTheta[RESOLVER_POS_ENCODER] = resolver1.ElecTheta;
	posEncMechTheta[RESOLVER_POS_ENCODER] = resolver1.MechTheta;

	// Position Sense Reversal
	//posEncElecTheta[RESOLVER_POS_ENCODER] = 1.0 - resolver1.ElecTheta;
	//posEncMechTheta[RESOLVER_POS_ENCODER] = 1.0 - resolver1.MechTheta;

#endif

	return;
}

//*****************************************************************************
//*****************************************************************************
//*****************************************************************************
//*****************************************************************************

void main(void)
{

	volatile int16 temp;

#ifdef FLASH
// Copy time critical code and Flash setup code to RAM
// The  RamfuncsLoadStart, RamfuncsLoadEnd, and RamfuncsRunStart
// symbols are created by the linker. Refer to the linker files.
    memcpy(&RamfuncsRunStart, &RamfuncsLoadStart, (Uint32)&RamfuncsLoadSize);
#endif

	//  Initialize System Control:
	// PLL, WatchDog, enable Peripheral Clocks
	// This example function is found in the F28M3Xx_SysCtrl.c file.
	InitSysCtrl();

	// Only used if running from FLASH
	// Note that the variable FLASH is defined by the compiler

#ifdef FLASH
// Call Flash Initialization to setup flash waitstates
// This function must reside in RAM
	InitFlash();	// Call the flash wrapper init function
#endif //(FLASH)

	// Waiting for enable flag set
	while (EnableFlag == FALSE)
	{
	  BackTicker++;
	}

	// Clear all interrupts and initialize PIE vector table:

	// Disable CPU interrupts
	DINT;

	// Initialize the PIE control registers to their default state.
	// The default state is all PIE interrupts disabled and flags
	// are cleared.
	// This function is found in the F28M3Xx_PieCtrl.c file.
	InitPieCtrl();

	// Disable CPU interrupts and clear all CPU interrupt flags:
	IER = 0x0000;
	IFR = 0x0000;
	// Initialize the PIE vector table with pointers to the shell Interrupt
	// Service Routines (ISR).
	// This will populate the entire table, even if the interrupt
	// is not used in this example.  This is useful for debug purposes.
	// The shell ISR routines are found in F28M3Xx_DefaultIsr.c.
	// This function is found in F28M3Xx_PieVect.c.
	InitPieVectTable();

// Timing sync for background loops
// Timer period definitions found in device specific PeripheralHeaderIncludes.h
	CpuTimer0Regs.PRD.all =  10000;		// A tasks
	CpuTimer1Regs.PRD.all =  20000;		// B tasks
	CpuTimer2Regs.PRD.all =  30000;	// C tasks

// Tasks State-machine init
	Alpha_State_Ptr = &A0;
	A_Task_Ptr = &A1;
	B_Task_Ptr = &B1;
	C_Task_Ptr = &C1;


// ****************************************************************************
// ****************************************************************************
//TODO PWM Configuration
// ****************************************************************************
// ****************************************************************************

    // Initialize PWM module
	EALLOW;
	CpuSysRegs.PCLKCR0.bit.TBCLKSYNC = 0;

	// *****************************************
	// Inverter PWM configuration
	// ****************************************
	/* By default on soprano the PWM clock is divided by 2
	 * ClkCfgRegs.PERCLKDIVSEL.bit.EPWMCLKDIV=1
	 * Deadband needs to be 2.0us => 10ns*200=2us
	 */
	PWM_1ch_UpDwnCnt_CNF(1,INV_PWM_TICKS,200);
	PWM_1ch_UpDwnCnt_CNF(2,INV_PWM_TICKS,200);
	PWM_1ch_UpDwnCnt_CNF(3,INV_PWM_TICKS,200);

	// **********************************************
	// Sigma Delta clock set up - pwm5
	// *********************************************
	/* Configure PWM5A for SD Clock i.e. 20Mhz
	 * 20 Mhz => 50ns => 50ns/10
	 */
	PWM_1ch_UpCnt_CNF(5,5);
	EPwm5Regs.CMPA.bit.CMPA=EPwm5Regs.TBPRD>>1;


	// **********************************************
	// Carrier clock for resolver - pwm6
	// *********************************************
	// Resolver PWM6 time base for injection
	PWM_1ch_UpDwnCnt_CNF(6,RESOLVER_PWM_TICKS,160);

	// ********************************************************************
	//PWM 11 for syncing up the SD filter windows with motor control PWMs
	// ********************************************************************
	PWM_1ch_UpCnt_CNF(11,INV_PWM_TICKS);

	// configure 2 and 3 as slaves
	EPwm2Regs.TBCTL.bit.SYNCOSEL = TB_SYNC_IN;
	EPwm2Regs.TBCTL.bit.PHSEN    = TB_ENABLE;
	EPwm2Regs.TBPHS.bit.TBPHS    = 2;
	EPwm2Regs.TBCTL.bit.PHSDIR   = TB_UP;

	EPwm3Regs.TBCTL.bit.SYNCOSEL = TB_SYNC_IN;
	EPwm3Regs.TBCTL.bit.PHSEN    = TB_ENABLE;
	EPwm3Regs.TBPHS.bit.TBPHS    = 2;
	EPwm3Regs.TBCTL.bit.PHSDIR   = TB_UP;

	TrigRegs.SYNCSELECT.bit.EPWM4SYNCIN = 0; 	 //EPwm1SyncOut

	EPwm4Regs.TBCTL.bit.SYNCOSEL = TB_SYNC_IN;
	EPwm5Regs.TBCTL.bit.SYNCOSEL = TB_SYNC_IN;

	EPwm6Regs.TBCTL.bit.SYNCOSEL = TB_SYNC_IN;
	EPwm6Regs.TBCTL.bit.PHSEN    = TB_ENABLE;
	EPwm6Regs.TBPHS.bit.TBPHS    = 2;
	EPwm6Regs.TBCTL.bit.PHSDIR   = TB_UP;

	TrigRegs.SYNCSELECT.bit.EPWM10SYNCIN = 0;  //EPwm1Sync Out
	EPwm10Regs.TBCTL.bit.SYNCOSEL        = TB_SYNC_IN;

	EPwm11Regs.TBCTL.bit.PHSEN  = TB_ENABLE;
	EPwm11Regs.TBPHS.bit.TBPHS  = 2;
	EPwm11Regs.TBCTL.bit.PHSDIR = TB_UP;

	EPwm11Regs.CMPC = (EPwm11Regs.TBPRD-640-640*0.5);
	EPwm11Regs.CMPA.bit.CMPA = 640+320+500; // 640+320;
	EPwm11Regs.CMPD = 0;

	// ***********************************
	// Set up GPIOs for PWM functions
	// **************************************
	InitEPwm1Gpio();
	InitEPwm2Gpio();
	InitEPwm3Gpio();
	InitEPwm4Gpio();
	InitEPwm5Gpio();

	EDIS;

// ****************************************************
// Initialize DATALOG module
// ****************************************************
	DLOG_4CH_F_init(&dlog_4ch1);
	dlog_4ch1.input_ptr1 = &DlogCh1;	//data value
	dlog_4ch1.input_ptr2 = &DlogCh2;
	dlog_4ch1.input_ptr3 = &DlogCh3;
	dlog_4ch1.input_ptr4 = &DlogCh4;
	dlog_4ch1.output_ptr1 = &DBUFF_4CH1[0];
	dlog_4ch1.output_ptr2 = &DBUFF_4CH2[0];
	dlog_4ch1.output_ptr3 = &DBUFF_4CH3[0];
	dlog_4ch1.output_ptr4 = &DBUFF_4CH4[0];
	dlog_4ch1.size = 200;
	dlog_4ch1.pre_scalar = 5;
	dlog_4ch1.trig_value = 0.01;
	dlog_4ch1.status = 2;
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

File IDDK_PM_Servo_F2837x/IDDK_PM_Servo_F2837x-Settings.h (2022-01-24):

#ifndef PROJ_INCLUDE_H
#define PROJ_INCLUDE_H

/*-------------------------------------------------------------------------------
Include project specific include files.
-------------------------------------------------------------------------------*/
// define math type as float(1)
#define   MATH_TYPE      1
#include "IQmathLib.h"
#include "F28x_Project.h"

#include "smopos.h"       		// Include header for the SMOPOS object 
#include "smopos_const.h"       // Include header for the SMOPOS object
#include "park.h"       		// Include header for the PARK object 
#include "ipark.h"       		// Include header for the IPARK object 
#include "pi.h"       			// Include header for the PIDREG3 object 
#include "clarke.h"         	// Include header for the CLARKE object 
#include "svgen.h"		       	// Include header for the SVGENDQ object 
#include "rampgen.h"        	// Include header for the RAMPGEN object 
#include "rmp_cntl.h"       	// Include header for the RMPCNTL object 
#include "volt_calc.h"      	// Include header for the PHASEVOLTAGE object 
#include "speed_est.h"          // Include header for the SPEED_ESTIMATION object 
#include "speed_fr.h"			// Include header for the SPEED_MEAS_QEP object
#include "resolver.h"
#include "pid_grando.h"
#include "pid_reg3.h"
#include <math.h>

#include "DLOG_4CH_F.h"

#include "F2837xD_sdfm_drivers.h"
#include "Resolver_Float.h"

#include "F2837x_QEP_Module.h"

/*------------------------------------------------------------------------------
Following is the list of the Build Level choices.
------------------------------------------------------------------------------*/
#define LEVEL1  1      		// Module check out (do not connect the motors)
#define LEVEL2  2           // Verify ADC, park/clarke, calibrate the offset and speed measurement
#define LEVEL3  3           // Verify closed current(torque) loop and its PIs
#define LEVEL4  4           // Verify speed loop and speed PID
#define LEVEL5  5           // Verify position loop

/*------------------------------------------------------------------------------
This line sets the BUILDLEVEL to one of the available choices.
------------------------------------------------------------------------------*/
#define   BUILDLEVEL LEVEL2

/*------------------------------------------------------------------------------
Following is the list of Current sense options
------------------------------------------------------------------------------*/
#define SHUNT_CURRENT_SENSE 1
#define LEM_CURRENT_SENSE   2
#define SD_CURRENT_SENSE    3

/*------------------------------------------------------------------------------
This line sets the CURRENT_SENSE to user's choice from the above.
------------------------------------------------------------------------------*/
#define CURRENT_SENSE LEM_CURRENT_SENSE

/*------------------------------------------------------------------------------
Following is the list of Position Encoder options
------------------------------------------------------------------------------*/
// Select Position Feedback Option
#define QEP_POS_ENCODER 1
#define RESOLVER_POS_ENCODER 2
#define BISS_POS_ENCODER 3
#define SINCOS_POS_ENCODER 4
#define ENDAT_POS_ENCODER 5

/*------------------------------------------------------------------------------
This line sets the POSITION_ENCODER to user's choice from the above.
------------------------------------------------------------------------------*/
#define POSITION_ENCODER QEP_POS_ENCODER

#ifndef BUILDLEVEL
#error  Critical: BUILDLEVEL must be defined !!
#endif  // BUILDLEVEL
//------------------------------------------------------------------------------


#ifndef TRUE
#define FALSE 0
#define TRUE  1
#endif

#define PI 3.14159265358979

// Define the system frequency (MHz)
#if (DSP2803x_DEVICE_H==1)
#define SYSTEM_FREQUENCY 60
#elif (DSP280x_DEVICE_H==1)
#define SYSTEM_FREQUENCY 100
#elif (F28_2837xD==1)
#define SYSTEM_FREQUENCY 200
#endif

// Timer definitions based on System Clock
// 150 MHz devices
#define		mSec0_5		0.5*SYSTEM_FREQUENCY*1000		// 0.5 mS
#define		mSec1		1*SYSTEM_FREQUENCY*1000		// 1.0 mS
#define		mSec2		2.0*SYSTEM_FREQUENCY*1000		// 2.0 mS
#define		mSec5		5*SYSTEM_FREQUENCY*1000		// 5.0 mS
#define		mSec7_5		7.5*SYSTEM_FREQUENCY*1000		// 7.5 mS
#define		mSec10		10*SYSTEM_FREQUENCY*1000		// 10 mS
#define		mSec20		20*SYSTEM_FREQUENCY*1000		// 20 mS
#define		mSec50		50*SYSTEM_FREQUENCY*1000		// 50 mS
#define		mSec100		100*SYSTEM_FREQUENCY*1000		// 100 mS
#define		mSec500		500*SYSTEM_FREQUENCY*1000	// 500 mS
#define		mSec1000	1000*SYSTEM_FREQUENCY*1000	// 1000 mS

// Define the ISR frequency (kHz)
#define ISR_FREQUENCY 10
#define INV_PWM_TICKS  ((SYSTEM_FREQUENCY/2.0)/ISR_FREQUENCY)*1000
#define INV_PWM_TBPRD INV_PWM_TICKS/2
#define INV_PWM_HALF_TBPRD INV_PWM_TICKS/4
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

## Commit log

2021-08-03 Create CONTROLLER BOARD
2021-08-19 Controller Board Altium Documents
    In this file, you can see the Altium documents for the Control Board. You can reach the schematics, PCB, Gerber files. Keep in mind that you can also see the schematics from the uploaded Schematics P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
    Each sub-schematic is a part of the whole system. You can refer to "Block Diagram" for better understanding.
    [AltiumProject.PrjPcb, Block Diagram.SchDoc, CAN.SchDoc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]
2021-08-19 Power Board Altium Documents
    In this file, you can see the Altium Documents for the power board. You can see the schematics and PCB design.
    [Circuit.SchDoc, DCDC CONV.SchDoc, Gate Drives.SchDoc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]
2021-08-19 Add files via upload
    This document is a brief explanation of the project where I underlined the reasons and working principles of the circuits. I recommend you to have a look at this document before going into detail.
2021-08-19 Project Schematics on PDF
